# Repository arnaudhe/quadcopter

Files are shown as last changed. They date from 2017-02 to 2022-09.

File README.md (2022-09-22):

# Quadcopter

DIY quadcopter based on ESP32-WROOM



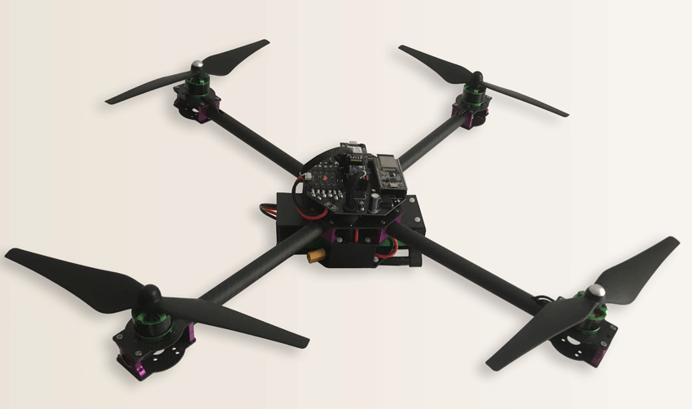
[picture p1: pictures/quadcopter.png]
Quadcopter picture Quadcopter


## Overview

### Architecture overview

```mermaid
  flowchart LR;
    subgraph QUADCOPTER
      BATTERY--supply-->Flight_controller
      BATTERY--supply-->GIMBAL
      HCSR04<--pulse-->ESP32
      subgraph Flight_controller
        MPU6050--I2C-->ESP32
        HMC5883L--I2C-->ESP32
        BMP280--I2C-->ESP32
        ESP32--DSHOT-->ESC
        ESP32--SPI-->SI4432
      end
      subgraph Motors
        ESC--3-->FRONT_RIGHT_MOTOR
        ESC--3-->FRONT_LEFT_MOTOR
        ESC--3-->REAR_RIGHT_MOTOR
        ESC--3-->REAR_LEFT_MOTOR
      end
      subgraph Video
        direction TB
        ESP32--PWM-->GIMBAL
        ESP32--TCP-->CAMERA
        CAMERA--Analog-->VIDEO_TX
        GIMBAL--supply-->VIDEO_TX
      end
      GPS--UART-->ESP32
    end
      subgraph Base_Station
        XBOX_REMOTE--USB-->LAPTOP
        LAPTOP<--USB-->RADIO_DONGLE
        VIDEO_RX--USB-->LAPTOP
      end
      RADIO_DONGLE-.433 MHz FSK.->SI4432
      LAPTOP-.WIFI.->ESP32
      VIDEO_TX-.5,8GHz.->VIDEO_RX
```

### Sensors

* Attitude sensing is based on MPU6050 (accelerometer + gyroscope) and HMC5883L (magnetometer), computed through a [Madgwick Filter](https://x-io.co.uk/open-source-imu-and-ahrs-algorithms/)
* Height sensing is based on vertical linear acceleration (output of attitude filter), a BMP180 (barometer) and a HCSR04 (ultrasound range sensor), computed through a [Kalman filter](https://en.wikipedia.org/wiki/Kalman_filter)
* Position sensing is base on horizontal linear acceleration (output of attitude filter) and a GPS, computed through a Kalman filter [Kalman filter](https://en.wikipedia.org/wiki/Kalman_filter)

cf. [documents](https://github.com/arnaudhe/quadcopter/tree/master/documents) for more details

### Controllers

* Attitude controller (manual mode) is based on a 4-dimensions [PID](https://en.wikipedia.org/wiki/PID_controller) (roll, pitch, yaw, height)
* Position controller (autonomous mode) is based on a 3-dimensions [PID](https://en.wikipedia.org/wiki/PID_controller) (x, y, z) which drives attitude controller

BLDC motors control is based on a commercial 4-in-1 ESC (electronic speed controller)

cf. [documents](https://github.com/arnaudhe/quadcopter/tree/master/documents) for more details

### Camera

The quadcopter is designed to support a [YI action camera](https://www.yitechnology.com/yi-action-camera), hold on a [2D Gimbal](https://hobbyking.com/fr_fr/tarot-t-2d-v2-xiaomi-yi-sports-camera-brushless-camera-gimbal-and-zyx22-controller.html).

The camera has:
* A TCP interface which supports json commands (take a picture, start recording, list files, ...)
* A streaming RTSP server which can be used for live video preview

The gimbal angles can be driven by the ESP32 through a serial interface.

### Communication

Communication between base station (computer or remote) is based on a shared data model, definied in a json file.

The data model ressources are implemented by the quadcopter and can be read/written/notified via:
* a json protocol (better for debug, high bandwith medium)
* a binary protocol (better for release, low bandwidth medium)

Two communications media are supported by the quadcopter:
* wifi (low range, hight bandwidth)
* FSK (longer range, low bandwidth)

```mermaid
  flowchart TD;
      subgraph Flight controller
      ESP32<-->WIFI;
      ESP32<-->RADIO;
      end
      WIFI--TCP/JSON-->CAMERA;
      CAMERA--Analog Video-->VTX
      VTX-->BASE_STATION
      WIFI<--UDP/JSON-->BASE_STATION
      RADIO<--FSK/BINARY-->BASE_STATION
```

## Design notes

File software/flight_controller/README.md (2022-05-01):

# Flight Controller

## Overview

The flight controller firmware runs on a ESP32, on a ESP32-WROOM development board.

This boards embeds an ESP32-VROOM module (which contains ESP32 MCU + wifi + BLE + flash), a power supply, a usb-serial interface, and a micro-USB port.

The project is based on Espressif's official [ESP-IDF SDK](https://github.com/espressif/esp-idf), which comes with many components (FreeRTOS, LwIP, utilities, ...). This third-party sdk is actually integrated as a git sumbodule.

## Setup

Flight controller SDK setup is managed by parent folder `software`, refer to its README

## Build, flash, monitor

### Setup the environement

```
# source ../env.sh
```

### Build

```
# idf.py build
```

### Flash

```
# idf.py flash [-p <port>]
```

### Monitor

```
# idf.py monitor [-p <port>]
```
Hit `ctrl + $` to exit

You can alternatively use any serial port util at 921600 bauds

## Visual Studio Code integration

Previous commands are configured as Visual Studio Code tasks.

Refer to parent folder READLE to setup Visual Studio Code and run those tasks

Then, hit `cmd + shift + B` to build the project. The errors and warnings should be highlighted in the "problems" tab.

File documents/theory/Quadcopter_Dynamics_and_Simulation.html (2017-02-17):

# Andrew Gibiansky :: Math → [Code] (http://andrew.gibiansky.com/)

# Quadcopter Dynamics and Simulation

Friday, November 23, 2012

# Introduction

A helicopter is a flying vehicle which uses rapidly spinning rotors to push air downwards, thus creating a thrust force keeping the helicopter aloft. Conventional helicopters have two rotors. These can be arranged as two coplanar rotors both providing upwards thrust, but spinning in opposite directions (in order to balance the torques exerted upon the body of the helicopter). The two rotors can also be arranged with one main rotor providing thrust and a smaller side rotor oriented laterally and counteracting the torque produced by the main rotor. However, these configurations require complicated machinery to control the direction of motion; a swashplate is used to change the angle of attack on the main rotors. In order to produce a torque the angle of attack is modulated by the location of each rotor in each stroke, such that more thrust is produced on one side of the rotor plane than the other. The complicated design of the rotor and swashplate mechanism presents some problems, increasing construction costs and design complexity.

A quadrotor helicopter (quadcopter) is a helicopter which has four equally spaced rotors, usually arranged at the corners of a square body. With four independent rotors, the need for a swashplate mechanism is alleviated. The swashplate mechanism was needed to allow the helicopter to utilize more degrees of freedom, but the same level of control can be obtained by adding two more rotors.

The development of quadcopters has stalled until very recently, because controlling four independent rotors has proven to be incredibly difficult and impossible without electronic assistance. The decreasing cost of modern microprocessors has made electronic and even completely autonomous control of quadcopters feasible for commercial, military, and even hobbyist purposes.

Quadcopter control is a fundamentally difficult and interesting problem. With six degrees of freedom (three translational and three rotational) and only four independent inputs (rotor speeds), quadcopters are severely underactuated. In order to achieve six degrees of freedom, rotational and translational motion are coupled. The resulting dynamics are highly nonlinear, especially after accounting for the complicated aerodynamic effects. Finally, unlike ground vehicles, helicopters have very little friction to prevent their motion, so they must provide their own damping in order to stop moving and remain stable. Together, these factors create a very interesting control problem. We will present a very simplified model of quadcopter dynamics and design controllers for our dynamics to follow a designated trajectory. We will then test our controllers with a numerical simulation of a quadcopter in flight.

# Quadcopter Dynamics

We will start deriving quadcopter dynamics by introducing the two frames in which will operate. The inertial frame is defined by the ground, with gravity pointing in the negative zz direction. The body frame is defined by the orientation of the quadcopter, with the rotor axes pointing in the positive zz direction and the arms pointing in the xx and yy directions.

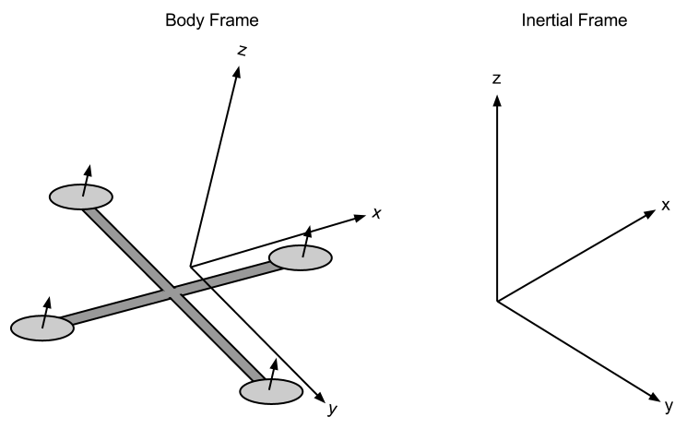
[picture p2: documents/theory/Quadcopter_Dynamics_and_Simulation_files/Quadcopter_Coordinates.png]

Quadcopter Body Frame and Inertial Frame

## Kinematics

Before delving into the physics of quadcopter motion, let us formalize the kinematics in the body and inertial frames. We define the position and velocity of the quadcopter in the inertial frame as x=(x,y,z)Tx=(x,y,z)T and x˙=(x˙,y˙,z˙)Tx˙=(x˙,y˙,z˙)T, respectively. Similarly, we define the roll, pitch, and yaw angles in the body frame as θ=(ϕ,θ,ψ)Tθ=(ϕ,θ,ψ)T, with corresponding angular velocities equal to θ˙=(ϕ˙,θ˙,ψ˙)Tθ˙=(ϕ˙,θ˙,ψ˙)T. However, note that the angular velocity vector ω≠θ˙ω≠θ˙. The angular velocity is a vector pointing along the axis of rotation, while θ˙θ˙ is just the time derivative of yaw, pitch, and roll. In order to convert these angular velocities into the angular velocity vector, we can use the following relation:

ω=⎡⎣⎢⎢⎢1000cϕ−sϕ−sθcθsϕcθcϕ⎤⎦⎥⎥⎥θ˙ω=[10−sθ0cϕcθsϕ0−sϕcθcϕ]θ˙

where ωω is the angular velocity vector in the body frame.

We can relate the body and inertial frame by a rotation matrix RR which goes from the body frame to the inertial frame. This matrix is derived by using the ZYZ Euler angle conventions and successively “undoing” the yaw, pitch, and roll.

R=⎡⎣⎢⎢⎢cϕcψ−cθsϕsψcθcψsϕ+cϕsψsϕsθ−cψsϕ−cϕcθsψcϕcθcψ−sϕsψcϕsθsθsψ−cψsθcθ⎤⎦⎥⎥⎥R=[cϕcψ−cθsϕsψ−cψsϕ−cϕcθsψsθsψcθcψsϕ+cϕsψcϕcθcψ−sϕsψ−cψsθsϕsθcϕsθcθ]

For a given vector v⃗ v→ in the body frame, the corresponding vector is given by Rv⃗ Rv→ in the inertial frame.

## Physics

In order to properly model the dynamics of the system, we need an understanding of the physical properties that govern it. We will begin with a description of the motors being used for our quadcopter, and then use energy considerations to derive the forces and thrusts that these motors produce on the entire quadcopter. All motors on the quadcopter are identical, so we can analyze a single one without loss of generality. Note that adjacent propellers, however, are oriented opposite each other; if a propeller is spinning “clockwise”, then the two adjacent ones will be spinning “counter-clockwise”, so that torques are balanced if all propellers are spinning at the same rate.

### Motors

Brushless motors are used for all quadcopter applications. For our electric motors, the torque produced is given by

τ=Kt(I−I0)τ=Kt(I−I0)

where ττ is the motor torque, II is the input current, I0I0 is the current when there is no load on the motor, and KtKt is the torque proportionality constant. The voltage across the motor is the sum of the back-EMF and some resistive loss:

V=IRm+KvωV=IRm+Kvω

where VV is the voltage drop across the motor, RmRm is the motor resistance, ωω is the angular velocity of the motor, and KvKv is a proportionality constant (indicating back-EMF generated per RPM). We can use this description of our motor to calculate the power it consumes. The power is

P=IV=(τ+KtI0)(KtI0Rm+τRm+KtKvω)Kt2P=IV=(τ+KtI0)(KtI0Rm+τRm+KtKvω)Kt2

For the purposes of our simple model, we will assume a negligible motor resistance. Then, the power becomes proportional to the angular velocity:

P≈(τ+KtI0)KvωKtP≈(τ+KtI0)KvωKt

Further simplifying our model, we assume that KtI0≪τKtI0≪τ. This is not altogether unreasonable, since I0I0 is the current when there is no load, and is thus rather small. In practice, this approximation holds well enough. Thus, we obtain our final, simplified equation for power:

P≈KvKtτω.P≈KvKtτω.

### Forces

The power is used to keep the quadcopter aloft. By conservation of energy, we know that the energy the motor expends in a given time period is equal to the force generated on the propeller times the distance that the air it displaces moves (P⋅dt=F⋅dxP⋅dt=F⋅dx). Equivalently, the power is equal to the thrust times the air velocity (P=FdxdtP=Fdxdt).

P=TvhP=Tvh

We assume vehicle speeds are low, so vhvh is the air velocity when hovering. We also assume that the free stream velocity, v∞v∞, is zero (the air in the surrounding environment is stationary relative to the quadcopter). Momentum theory gives us the equation for hover velocity as a function of thrust,

vh=T2ρA‾‾‾‾‾√vh=T2ρA

where ρρ is the density of the surrounding air and AA is the area swept out by the rotor. Using our simplified equation for power, we can then write

P=KvKtτω=KvKτKtTω=T322ρA‾‾‾‾√.P=KvKtτω=KvKτKtTω=T322ρA.

Note that in the general case, τ=r⃗ ×F⃗ τ=r→×F→; in this case, the torque is proportional to the thrust TT by some constant ratio KτKτ determined by the blade configuration and parameters. Solving for the thrust magnitude TT, we obtain that thrust is proportional to the square of angular velocity of the motor:

T=(KvKτ2ρA‾‾‾‾√Ktω)2=kω2T=(KvKτ2ρAKtω)2=kω2

where kk is some appropriately dimensioned constant. Summing over all the motors, we find that the total thrust on the quadcopter (in the body frame) is given by

TB=∑i=14Ti=k⎡⎣⎢⎢⎢00∑ωi2⎤⎦⎥⎥⎥.TB=∑i=14Ti=k[00∑ωi2].

In addition to the thrust force, we will model friction as a force proportional to the linear velocity in each direction. This is a highly simplified view of fluid friction, but will be sufficient for our modeling and simulation. Our global drag forces will be modeled by an additional force term

FD=⎡⎣⎢⎢−kdx˙−kdy˙−kdz˙⎤⎦⎥⎥FD=[−kdx˙−kdy˙−kdz˙]

If additional precision is desired, the constant kdkd can be separated into three separate friction constants, one for each direction of motion. If we were to do this, we would want to model friction in the body frame rather than the inertial frame.

### Torques

Now that we have computed the forces on the quadcopter, we would also like to compute the torques. Each rotor contributes some torque about the body zz axis. This torque is the torque required to keep the propeller spinning and providing thrust; it creates the instantaneous angular acceleration and overcomes the frictional drag forces. The drag equation from fluid dynamics gives us the frictional force:

FD=12ρCDAv2.FD=12ρCDAv2.

where ρρ is the surrounding fluid density, AA is the reference area (propeller cross-section, not area swept out by the propeller), and CDCD is a dimensionless constant. This, while only accurate in some in some cases, is good enough for our purposes. This implies that the torque due to drag is given by

τD=12RρCDAv2=12RρCDA(ωR)2=bω2τD=12RρCDAv2=12RρCDA(ωR)2=bω2

where ωω is the angular velocity of the propeller, RR is the radius of the propeller, and bb is some appropriately dimensioned constant. Note that we’ve assumed that all the force is applied at the tip of the propeller, which is certainly inaccurate; however, the only result that matters for our purposes is that the drag torque is proportional to the square of the angular velocity. We can then write the complete torque about the zz axis for the iith motor:

τz=bω2+IMω˙τz=bω2+IMω˙

where IMIM is the moment of inertia about the motor zz axis, ω˙ω˙ is the angular acceleration of the propeller, and bb is our drag coefficient. Note that in steady state flight (i.e. not takeoff or landing), ω˙≈0ω˙≈0, since most of the time the propellers will be maintaining a constant (or almost constant) thrust and won’t be accelerating. Thus, we ignore this term, simplifying the entire expression to

τz=(−1)i+1bωi2.τz=(−1)i+1bωi2.

where the (−1)i+1(−1)i+1 term is positive for the iith propeller if the propeller is spinning clockwise and negative if it is spinning counterclockwise. The total torque about the zz axis is given by the sum of all the torques from each propeller:

τψ=b(ω12−ω22+ω32−ω42)τψ=b(ω12−ω22+ω32−ω42)

The roll and pitch torques are derived from standard mechanics. We can arbitrarily choose the i=1i=1 and i=3i=3 motors to be on the roll axis, so

τϕ=∑r×T=L(kω12−kω32)=Lk(ω12−ω32)τϕ=∑r×T=L(kω12−kω32)=Lk(ω12−ω32)

Correspondingly, the pitch torque is given by a similar expression

τθ=Lk(ω22−ω42)τθ=Lk(ω22−ω42)

where LL is the distance from the center of the quadcopter to any of the propellers. All together, we find that the torques in the body frame are

τB=⎡⎣⎢⎢⎢Lk(ω12−ω32)Lk(ω22−ω42)b(ω12−ω22+ω32−ω42)⎤⎦⎥⎥⎥τB=[Lk(ω12−ω32)Lk(ω22−ω42)b(ω12−ω22+ω32−ω42)]

The model we’ve derived so far is highly simplified. We ignore a multitude of advanced effects that contribute to the highly nonlinear dynamics of a quadcopter. We ignore rotational drag forces (our rotational velocities are relatively low), blade flapping (deformation of propeller blades due to high velocities and flexible materials), surrounding fluid velocities (wind), etc. With that said, we now have all the parts necessary to write out the dynamics of our quadcopter.

### Equations of Motion

In the inertial frame, the acceleration of the quadcopter is due to thrust, gravity, and linear friction. We can obtain the thrust vector in the inertial frame by using our rotation matrix RR to map the thrust vector from the body frame to the inertial frame. Thus, the linear motion can be summarized as

mx¨=⎡⎣⎢⎢00−mg⎤⎦⎥⎥+RTB+FDmx¨=[00−mg]+RTB+FD

where x⃗ x→ is the position of the quadcopter, gg is the acceleration due to gravity, FDFD is the drag force, and TBTB is the thrust vector in the body frame. While it is convenient to have the linear equations of motion in the inertial frame, the rotational equations of motion are useful to us in the body frame, so that we can express rotations about the center of the quadcopter instead of about our inertial center. We derive the rotational equations of motion from Euler’s equations for rigid body dynamics. Expressed in vector form, Euler’s equations are written as

Iω˙+ω×(Iω)=τIω˙+ω×(Iω)=τ

where ωω is the angular velocity vector, II is the inertia matrix, and ττ is a vector of external torques. We can rewrite this as

ω˙=⎡⎣⎢⎢⎢ω˙xω˙yω˙z⎤⎦⎥⎥⎥=I−1(τ−ω×(Iω)).ω˙=[ω˙xω˙yω˙z]=I−1(τ−ω×(Iω)).

We can model our quadcopter as two thin uniform rods crossed at the origin with a point mass (motor) at the end of each. With this in mind, it’s clear that the symmetries result in a diagonal inertia matrix of the form

I=⎡⎣⎢⎢⎢Ixx000Iyy000Izz⎤⎦⎥⎥⎥.I=[Ixx000Iyy000Izz].

Therefore, we obtain our final result for the body frame rotational equations of motion

ω˙=⎡⎣⎢⎢⎢τϕIxx−1τθIyy−1τψIzz−1⎤⎦⎥⎥⎥−⎡⎣⎢⎢⎢⎢Iyy−IzzIxxωyωzIzz−IxxIyyωxωzIxx−IyyIzzωxωy⎤⎦⎥⎥⎥⎥ω˙=[τϕIxx−1τθIyy−1τψIzz−1]−[Iyy−IzzIxxωyωzIzz−IxxIyyωxωzIxx−IyyIzzωxωy]

# Simulation

Now that we have complete equations of motion describing the dynamics of the system, we can create a simulation environment in which to test and view the results of various inputs and controllers. Although more advanced methods are available, we can quickly write a simulator which utilizes Euler’s method for solving differential equations to evolve the system state. In MATLAB, this simulator would be written as follows.

% Simulation times, in seconds.
start_time = 0;
end_time = 10;
dt = 0.005;
times = start_time:dt:end_time;

% Number of points in the simulation.
N = numel(times);

% Initial simulation state.
x = [0; 0; 10];
xdot = zeros(3, 1);
theta = zeros(3, 1);

% Simulate some disturbance in the angular velocity.
% The magnitude of the deviation is in radians / second.
deviation = 100;
thetadot = deg2rad(2 * deviation * rand(3, 1) - deviation);

% Step through the simulation, updating the state.
for t = times
    % Take input from our controller.
    i = input(t);

    omega = thetadot2omega(thetadot, theta);

    % Compute linear and angular accelerations.
    a = acceleration(i, theta, xdot, m, g, k, kd);
    omegadot = angular_acceleration(i, omega, I, L, b, k);

    omega = omega + dt * omegadot;
    thetadot = omega2thetadot(omega, theta); 
    theta = theta + dt * thetadot;
    xdot = xdot + dt * a;
    x = x + dt * xdot;
end

We would then need functions to compute all of the physical forces and torques.

% Compute thrust given current inputs and thrust coefficient.
function T = thrust(inputs, k)
    % Inputs are values for ${\omega_i}^2$
    T = [0; 0; k * sum(inputs)];
end

% Compute torques, given current inputs, length, drag coefficient, and thrust coefficient.
function tau = torques(inputs, L, b, k)
    % Inputs are values for ${\omega_i}^2$
    tau = [
        L * k * (inputs(1) - inputs(3))
        L * k * (inputs(2) - inputs(4))
        b * (inputs(1) - inputs(2) + inputs(3) - inputs(4))
    ];
end

function a = acceleration(inputs, angles, xdot, m, g, k, kd)
    gravity = [0; 0; -g];
    R = rotation(angles);
    T = R * thrust(inputs, k);
    Fd = -kd * xdot;
    a = gravity + 1 / m * T + Fd;
end

function omegadot = angular_acceleration(inputs, omega, I, L, b, k)
    tau = torques(inputs, L, b, k);
    omegaddot = inv(I) * (tau - cross(omega, I * omega));
end

We would also need values for all of our physical constants, a function to compute the rotation matrix RR, and functions to convert from an angular velocity vector ωω to the derivatives of roll, pitch, and yaw and vice-versa. These are not shown. We can then draw the quadcopter in a three-dimensional visualization which is updated as the simulation is running.

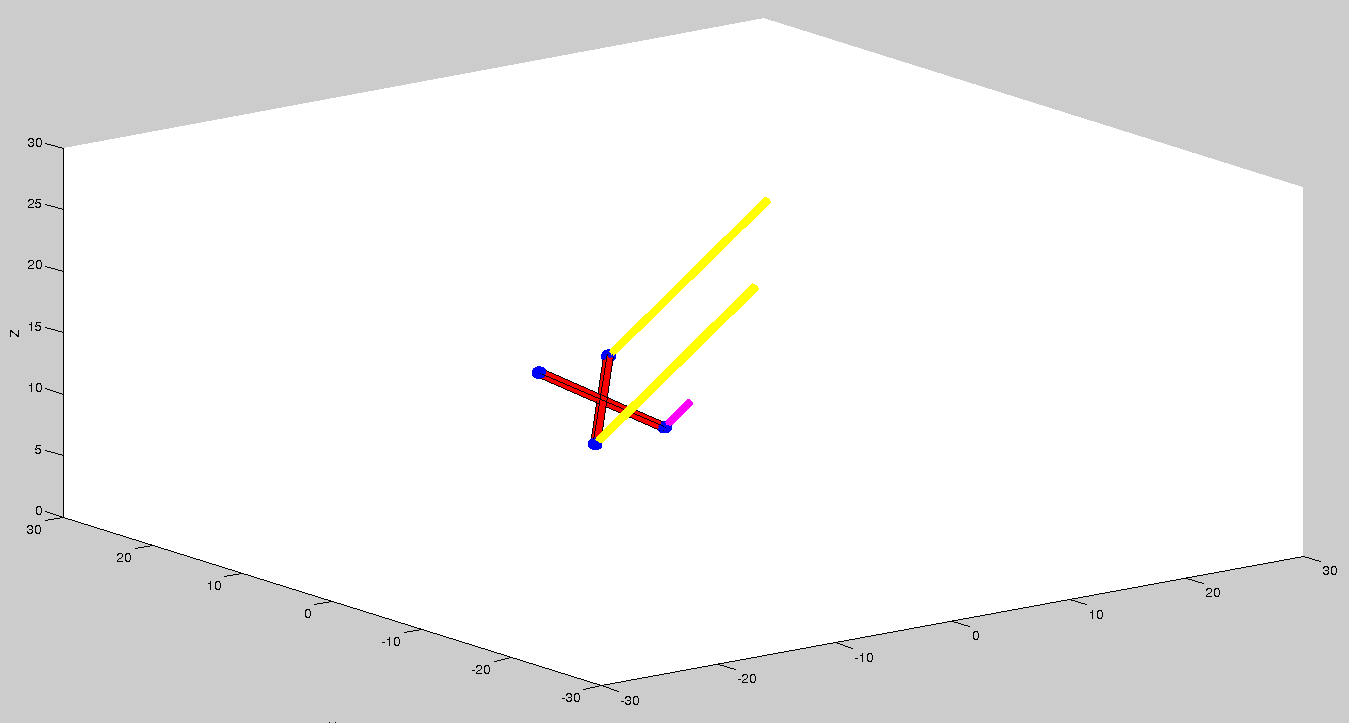
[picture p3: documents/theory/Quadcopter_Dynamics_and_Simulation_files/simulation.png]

Quadcopter Simulation. Bars above each propeller represent, roughly, relative thrust magnitudes.

# Control

The purpose of deriving a mathematical model of a quadcopter is to assist in developing controllers for physical quadcopters. The inputs to our system consist of the angular velocities of each rotor, since all we can control is the voltages across the motors. Note that in our simplified model, we only use the square of the angular velocities, ωi2ωi2, and never the angular velocity itself, ωiωi. For notational simplicity, let us introduce the inputs γi=ωi2γi=ωi2. Since we can set ωiωi, we can clearly set γiγi as well. With this, we can write our system as a first order differential equation in state space. Let x1x1 be the position in space of the quadcopter, x2x2 be the quadcopter linear velocity, x3x3 be the roll, pitch, and yaw angles, and x4x4 be the angular velocity vector. (Note that all of these are 3-vectors.) With these being our state, we can write the state space equations for the evolution of our state.

x1˙x2˙x3˙x4˙=x2=⎡⎣⎢⎢00−g⎤⎦⎥⎥+1mRTB+1mFD=⎡⎣⎢⎢⎢1000cϕ−sϕ−sθcθsϕcθcϕ⎤⎦⎥⎥⎥−1x4=⎡⎣⎢⎢⎢τϕIxx−1τθIyy−1τψIzz−1⎤⎦⎥⎥⎥−⎡⎣⎢⎢⎢⎢Iyy−IzzIxxωyωzIzz−IxxIyyωxωzIxx−IyyIzzωxωy⎤⎦⎥⎥⎥⎥x1˙=x2x2˙=[00−g]+1mRTB+1mFDx3˙=[10−sθ0cϕcθsϕ0−sϕcθcϕ]−1x4x4˙=[τϕIxx−1τθIyy−1τψIzz−1]−[Iyy−IzzIxxωyωzIzz−IxxIyyωxωzIxx−IyyIzzωxωy]

Note that our inputs are not used in these equations directly. However, as we will see, we can choose values for ττ and TT, and then solve for values of γiγi.

## PD Control

In order to control the quadcopter, we will use a PD control, with a component proportional to the error between our desired trajectory and the observed trajectory, and a component proportional to the derivative of the error. Our quadcopter will only have a gyro, so we will only be able to use the angle derivatives ϕ˙ϕ˙, θ˙θ˙, and ψ˙ψ˙ in our controller; these measured values will give us the derivative of our error, and their integral will provide us with the actual error. We would like to stabilize the helicopter in a horizontal position, so our desired velocities and angles will all be zero. Torques are related to our angular velocities by τ=Iθ¨τ=Iθ¨, so we would like to set the torques proportional to the output of our controller, with τ=Iu(t)τ=Iu(t). Thus,

⎡⎣⎢⎢⎢τϕτθτψ⎤⎦⎥⎥⎥=⎡⎣⎢⎢⎢⎢⎢−Ixx(Kdϕ˙+Kp∫T0ϕ˙dt)−Iyy(Kdθ˙+Kp∫T0θ˙dt)−Izz(Kdψ˙+Kp∫T0ψ˙dt)⎤⎦⎥⎥⎥⎥⎥[τϕτθτψ]=[−Ixx(Kdϕ˙+Kp∫0Tϕ˙dt)−Iyy(Kdθ˙+Kp∫0Tθ˙dt)−Izz(Kdψ˙+Kp∫0Tψ˙dt)]

We have previously derived the relationship between torque and our inputs, so we know that

τB=⎡⎣⎢⎢Lk(γ1−γ3)Lk(γ2−γ4)b(γ1−γ2+γ3−γ4)⎤⎦⎥⎥=⎡⎣⎢⎢⎢⎢⎢−Ixx(Kdϕ˙+Kp∫T0ϕ˙dt)−Iyy(Kdθ˙+Kp∫T0θ˙dt)−Izz(Kdψ˙+Kp∫T0ψ˙dt)⎤⎦⎥⎥⎥⎥⎥τB=[Lk(γ1−γ3)Lk(γ2−γ4)b(γ1−γ2+γ3−γ4)]=[−Ixx(Kdϕ˙+Kp∫0Tϕ˙dt)−Iyy(Kdθ˙+Kp∫0Tθ˙dt)−Izz(Kdψ˙+Kp∫0Tψ˙dt)]

This gives us a set of three equations with four unknowns. We can constrain this by enforcing the constraint that our inputs must keep the quadcopter aloft:

T=mg.T=mg.

Note that this equation ignores the fact that the thrust will not be pointed directly up. This will limit the applicability of our controller, but should not cause major problems for small deviations from stability. If we had a way of determining the current angle accurately, we could compensate. If our gyro is precise enough, we can integrate the values obtained from the gyro to get the angles θθ and ϕϕ. In this case, we can calculate the thrust necessary to keep the quadcopter aloft by projecting the thrust mgmg onto the inertial zz axis. We find that

Tproj=mgcosθcosϕTproj=mgcos⁡θcos⁡ϕ

Therefore, with a precise angle measurement, we can instead enforce the requirement that the thrust be equal to

T=mgcosθcosϕT=mgcos⁡θcos⁡ϕ

in which case the component of the thrust pointing along the positive zz axis will be equal to mgmg. We know that the thrust is proportional to a weighted sum of the inputs:

T=mgcosθcosϕ=k∑γi⟹∑γi=mgkcosθcosϕT=mgcos⁡θcos⁡ϕ=k∑γi⟹∑γi=mgkcos⁡θcos⁡ϕ

With this extra constraint, we have a set of four linear equations with four unknowns γiγi. We can then solve for each γiγi, and obtain the following input values:

γ1γ2γ3γ4=mg4kcosθcosϕ−2beϕIxx+eψIzzkL4bkL=mg4kcosθcosϕ+eψIzz4b−eθIyy2kL=mg4kcosθcosϕ−−2beϕIxx+eψIzzkL4bkL=mg4kcosθcosϕ+eψIzz4b+eθIyy2kLγ1=mg4kcos⁡θcos⁡ϕ−2beϕIxx+eψIzzkL4bkLγ2=mg4kcos⁡θcos⁡ϕ+eψIzz4b−eθIyy2kLγ3=mg4kcos⁡θcos⁡ϕ−−2beϕIxx+eψIzzkL4bkLγ4=mg4kcos⁡θcos⁡ϕ+eψIzz4b+eθIyy2kL

This is a complete specification for our PD controller. We can simulate this controller using our simulation environment. The controller drives the angular velocities and angles to zero.

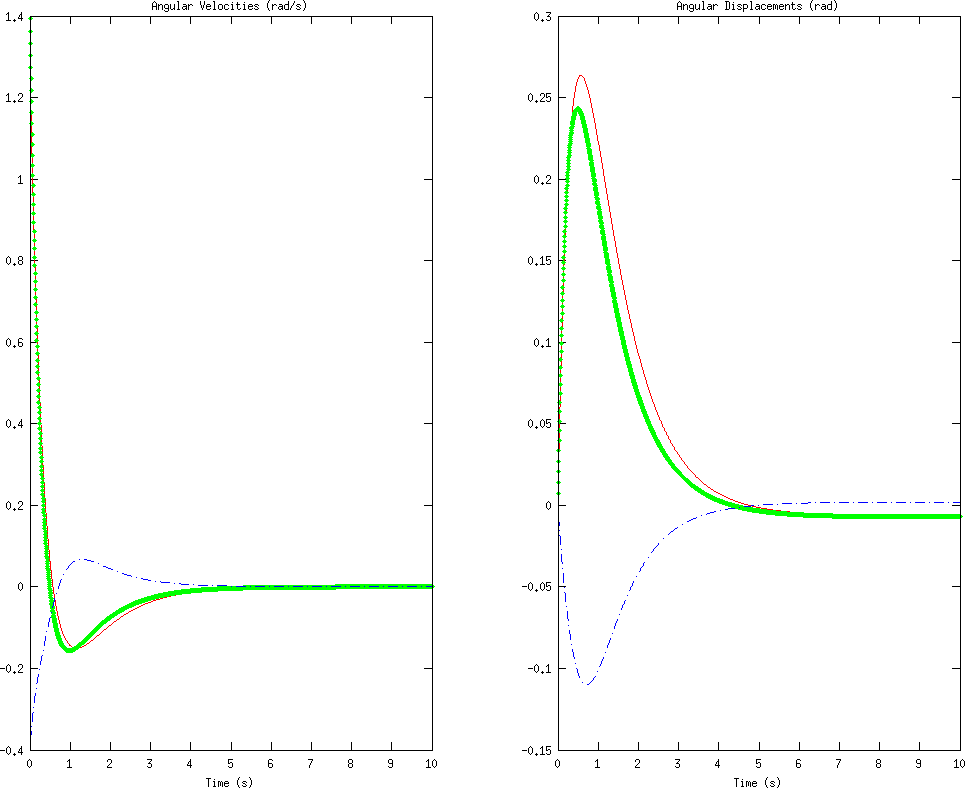
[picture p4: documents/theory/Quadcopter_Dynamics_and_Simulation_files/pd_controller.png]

Left: Angular velocities. Right: angular displacements. ϕϕ, θθ, ψψ are coded as red, green, and blue.

However, note that the angles are not completely driven to zero. The average steady state error (error after 10 seconds of simulation) is approximately 0.3∘∘. This is a common problem with using PD controllers for mechanical systems, and can be partially alleviated with a PID controller, as we will discuss in the next section.

In addition, note that since we are only controlling angular velocities, our positions and linear velocities do not converge to zero. However, the zz position will remain constant, because we have constrained the total vertical thrust to be such that it keeps the quadcopter perfectly aloft, without ascending or descending. However, this is really nothing more than a curiosity. With the limited sensing that we have available to us, there is nothing we can do to control the linear position and velocity of the quadcopter. While in theory we could compute the linear velocities and positions from the angular velocities, in practice the values will be so noisy as to be completely useless. Thus, we will restrict ourselves to just stabilizing the quadcopter angle and angular velocity. (Traditionally, navigation is done by a human, and stabilization is there simply to make control easier for the human operator.)

We have implemented this PD control for use in our simulation. The controller is implemented as a function which is given some state (corresponding to controller state, not system state) and the sensor inputs, and must compute the inputs γiγi and the updated state. The code for a PD control follows.

% Compute system inputs and updated state.
% Note that input = [$\gamma_1$, $\ldots$, $\gamma_4$]
function [input, state] = pd_controller(state, thetadot)
    % Controller gains, tuned by hand and intuition.
    Kd = 4;
    Kp = 3;

    % Initialize the integral if necessary.
    if ~isfield(state, 'integral')
        params.integral = zeros(3, 1);
    end

    % Compute total thrust
    total = state.m * state.g / state.k / (cos(state.integral(1)) * cos(state.integral(2)));

    % Compute errors
    e = Kd * thetadot + Kp * params.integral;

    % Solve for the inputs, $\gamma_i$
    input = error2inputs(params, accels, total);

    % Update the state
    params.integral = params.integral + params.dt .* thetadot;
end

## PID Control

PD controllers are nice in their simplicity and ease of implementation, but they are often inadequate for controlling mechanical systems. Especially in the presence of noise and disturbances, PD controllers will often lead to steady state error. A PID control is a PD control with another term added, which is proportional to the integral of the process variable. Adding an integral term causes any remaining steady-state error to build up and enact a change, so a PID controller should be able to track our trajectory (and stabilize the quadcopter) with a significantly smaller steady-state error. The equations remain identical to the ones presented in the PD case, but with an additional term in the error:

eϕeθeψ=Kdϕ˙+Kp∫T0ϕ˙dt+Ki∫T0∫T0ϕ˙dtdt=Kdθ˙+Kp∫T0θ˙dt+Ki∫T0∫T0θ˙dtdt=Kdψ˙+Kp∫T0ψ˙dt+Ki∫T0∫T0ψ˙dtdteϕ=Kdϕ˙+Kp∫0Tϕ˙dt+Ki∫0T∫0Tϕ˙dtdteθ=Kdθ˙+Kp∫0Tθ˙dt+Ki∫0T∫0Tθ˙dtdteψ=Kdψ˙+Kp∫0Tψ˙dt+Ki∫0T∫0Tψ˙dtdt

However, PID controls come with their own shortcomings. One problem that commonly occurs with a PID control is known as integral windup.

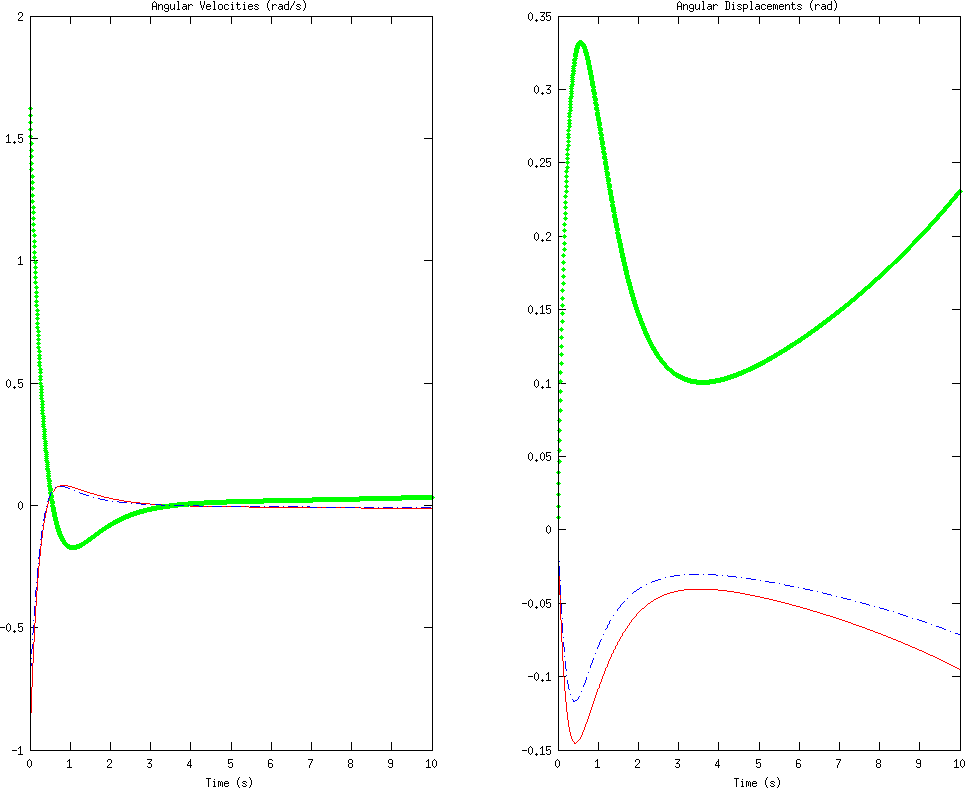
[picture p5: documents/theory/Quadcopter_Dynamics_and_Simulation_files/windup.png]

In some cases, integral wind-up can cause lengthy oscillations instead of settling. In other cases, wind-up may actually cause the system to become unstable, instead of taking longer to reach a steady state.

If there is a large disturbance in the process variable, this large disturbance is integrated over time, becoming a still larger control signal (due to the integral term). However, even once the system stabilizes, the integral is still large, thus causing the controller to overshoot its target. It may then begin a series of dieing down oscillations, become unstable, or simply take an incredibly long time to reach a steady state. In order to avoid this, we disable the integral function until we reach something close to the steady state. Once we are in a controllable region near the desired steady state, we turn on the integral function, which pushes the system towards a low steady-state error.

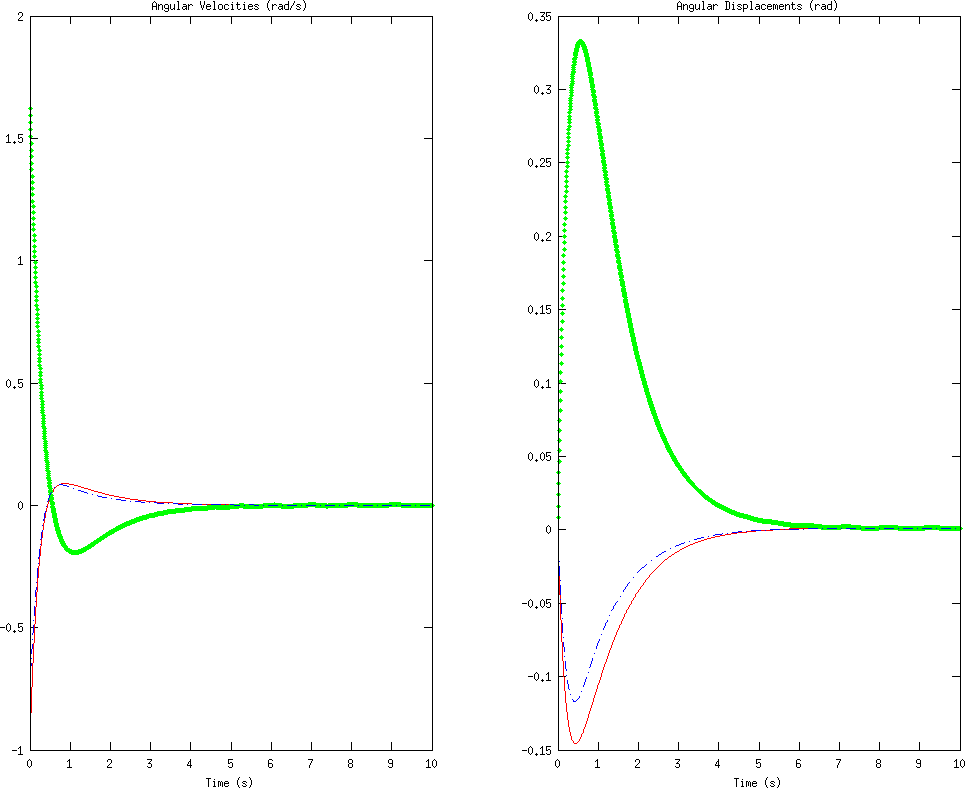
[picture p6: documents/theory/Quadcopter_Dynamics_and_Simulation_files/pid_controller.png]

With a properly implemented PID, we achieve an error of approximately 0.06∘∘ after 10 seconds.

We have implemented this PID control for use in simulation, in the same way as with the PD controller shown earlier. Note that there is an additional parameter to tune in a PID. The disturbances used for all the test cases are identical, shown to compare the controllers.

% Compute system inputs and updated state.
% Note that input = [$\gamma_1$, $\ldots$, $\gamma_4$]
function [input, state] = pid_controller(state, thetadot)
    % Controller gains, tuned by hand and intuition.
    Kd = 4;
    Kp = 3;
    Ki = 5.5;

    % Initialize the integral if necessary.
    if ~isfield(state, 'integral')
        params.integral = zeros(3, 1);
        params.integral2 = zeros(3, 1);
    end

    % Prevent wind-up
    if max(abs(params.integral2)) > 0.01
        params.integral2(:) = 0;
    end

    % Compute total thrust
    total = state.m * state.g / state.k / (cos(state.integral(1)) * cos(state.integral(2)));

    % Compute errors
    e = Kd * thetadot + Kp * params.integral - Ki * params.integral2;

    % Solve for the inputs, $\gamma_i$
    input = error2inputs(params, accels, total);

    % Update the state
    params.integral = params.integral + params.dt .* thetadot;
    params.integral2 = params.integral2 + params.dt .* params.integral;
end

## Automatic PID Tuning

Although PID control has the potential to perform very well, it turns out that the quality of the controller is highly dependent on the gain parameters. Tuning the parameters by hand may be quite difficult, as the ratios of the parameters is as important as the magnitudes of the parameters themselves; often, tuning parameters requires detailed knowledge of the system and an understanding of the conditions in which the PID control will be used. The parameters we chose previously were tuned by hand for good performance, simply by running simulations with many possibly disturbances and parameter values, and choosing something that worked reasonably well. This method is clearly suboptimal, not only because it can be very difficult and labor-intensive (and sometimes more or less impossible) but also because the resulting gains are not in any way guaranteed to be optimal or even close to optimal.

Ideally, we would be able to use an algorithm to analyze a system and output the “optimal” PID gains, for some reasonable definition of optimal. This problem has been studied in depth, and many methods have been proposed. Many of these methods require detailed knowledge of the system being modeled, and some rely on properties of the system, such as stability or linearity. The method we will use for choosing our PID parameters is a method known as extremum seeking.

Extremum seeking works exactly as the name implies. We define the “optimal” set of parameters as some vector θ⃗ =(Kp,Ki,Kd)θ→=(Kp,Ki,Kd) which minimizes some cost function J(θ⃗ )J(θ→). In our case, we would like to define a cost function that penalizes high error and error over extended durations of time. One candidate cost function is given by

J(θ⃗ )=1tf−to∫tft0e(t,θ⃗ )2dtJ(θ→)=1tf−to∫t0tfe(t,θ→)2dt

where e(t,θ⃗ )e(t,θ→) is the error in following some reference trajectory with some initial disturbance using a set of parameters θ⃗ θ→. Suppose we were able to somehow compute the gradient of this cost function, ∇J(θ⃗ )∇J(θ→). In that case, we could iteratively improve our parameter vector by defining a parameter update rule

θ⃗ (k+1)=θ⃗ (k)−α∇J(θ⃗ )θ→(k+1)=θ→(k)−α∇J(θ→)

where θ⃗ (k)θ→(k) is the parameter vector after kk iterations and αα is some step size which dictates how much we adjust our parameter vector at each step of the iteration. As k→∞k→∞, the cost function J(θ⃗ )J(θ→) will approach a local minimum in the space of PID parameters.

The question remains as to how we can estimate ∇J(θ⃗ )∇J(θ→). By definition,

∇J(θ⃗ )=(∂∂KpJ(θ⃗ ),∂∂KiJ(θ⃗ ),∂∂KdJ(θ⃗ )).∇J(θ→)=(∂∂KpJ(θ→),∂∂KiJ(θ→),∂∂KdJ(θ→)).

We know how to compute J(θ⃗ )J(θ→). Using this, we can approximate the derivative with respect to any of the gains numerically, simply by computing

∂∂KJ(θ⃗ )≈J(θ⃗ +δ⋅û K)−J(θ⃗ −δ⋅û K)2δ∂∂KJ(θ→)≈J(θ→+δ⋅u^K)−J(θ→−δ⋅u^K)2δ

where û Ku^K is the unit vector in the KK direction. As δ→0δ→0, this approximation becomes better. Using this approximation, we can minimize our cost function and achieve locally optimal PID parameters. We can start with randomly initialized positive weights, disturb the system in some set manner, evaluate J(θ⃗ )J(θ→) by simulating the system for different PID parameters, and then compute the gradient. Then, using the method of gradient descent, we can iteratively oprtimize our gains until we have some form of convergence.

The gradient descent method does, however, have several problems. First of all, although it finds a local minimum, that minimum is only guaranteed to be a local minimum - there may be other minima which are better global minima. In order to avoid choosing suboptimal local minima in the cost function, we repeat our optimization several times, and choose the best result. We initialize our PID parameters randomly, so each time we run the optimization we will get a different result. In addition, instead of choosing disturbance and then optimizing the response to that disturbance, we use several random disturbances at each iteration and use the average response to compute costs and gradients. This ensures that our parameters are general and not optimized for a specific disturbance. In addition, we vary the step size and the number of disturbances to try per iteration, in order to increase the sensitivity of our results as our iteration continues. We stop iterations when we detect a steady state, which we do by computing a linear regression on the most recent costs and iterating until the slope is statistically indistinguishable from zero using a 99% confidence interval.

Using our quadcopter simulation, we can define a function that computes the cost for a given set of PID parameters.

function J = cost(theta)
    % Create a controller using the given gains.
    control = controller('pid', theta(1), theta(2), theta(3));

    % Perform a simulation.
    data = simulate(control);

    % Compute the integral, $\frac{1}{t_f - t_0} \int_{t_0}^{t_f} e(t)^2 dt$
    t0 = 0;
    tf = 1;
    J = 1/(tf - t0) * sum(data.theta(data.t >= t0 & data.t <= tf) .^ 2) * data.dt;
end

We can use this function to approximate a derivative with respect to a gain:

% Compute derivative with respect to first parameter.
delta = 0.01;
var = [1, 0, 0];
derivative = (cost(theta + delta * var) - cost(theta - delta * var)) / (2 * delta);

We can then use our gradient descent method (with all modifications described above) to minimize the cost function and obtain a good set of PID parameters. We can verify that our tuning method is working by visualizing the cost function versus the iteration number, and seeing that the cost function is indeed going down and stabilizing at a local minimum.

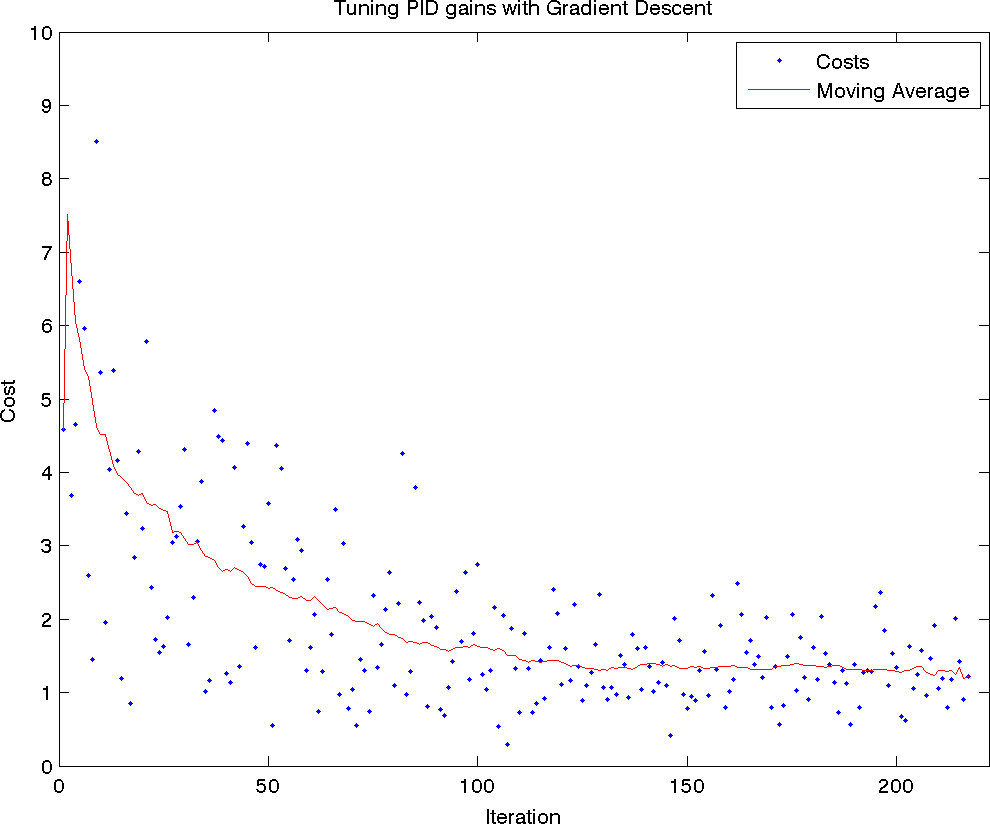
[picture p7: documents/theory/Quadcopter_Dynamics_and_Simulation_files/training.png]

Cost function plotted as a function of iteration number, along with moving average. Tuning stops when the slope of the moving average becomes statistically indistinguishable from zero with a 99% confidence interval.

We can compare the manually-chosen PID parameters with those designed by the algorithm.

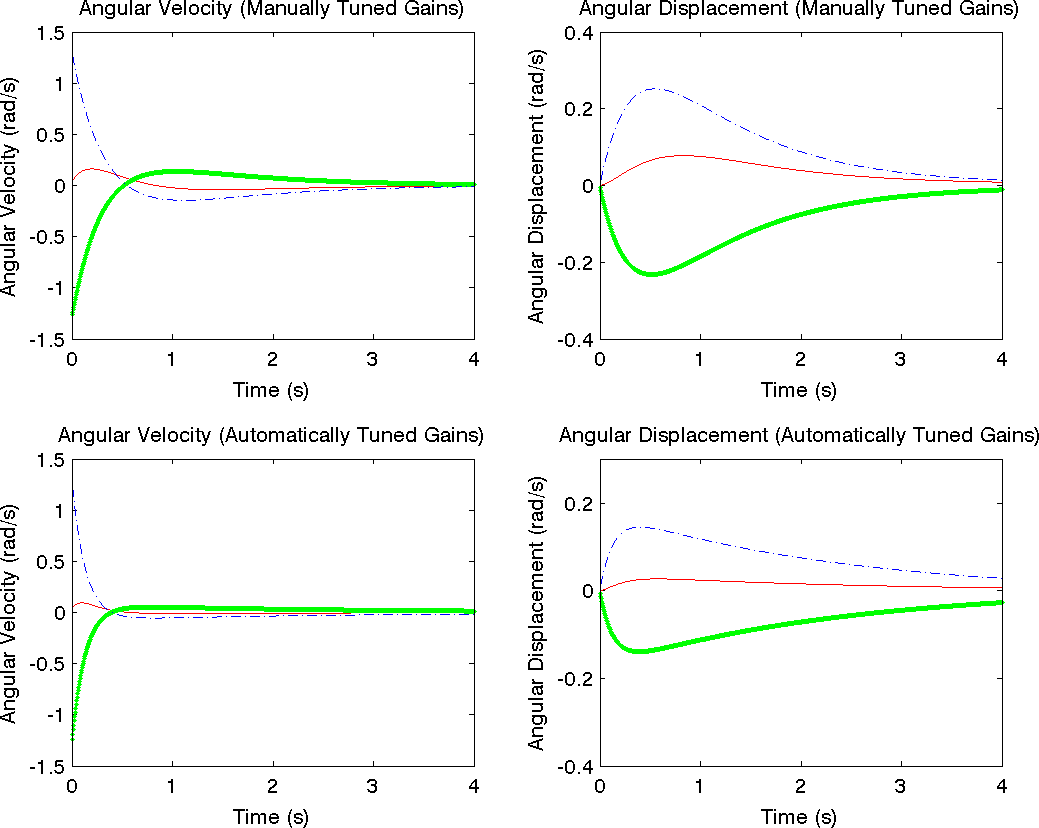
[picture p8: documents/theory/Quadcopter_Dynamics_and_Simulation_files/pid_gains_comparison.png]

Top: Angular velocities and angular displacements, using manually tuned PID controller. Bottom: Angular velocities and angular displacements, using automatically tuned PID controller.

The automatically-chosen PID parameters do significantly better overall. They have significantly smaller swings in value, overshoot significantly less, and converge faster. However, the error in the angular displacement takes longer to converge to zero with the automatically tuned parameters than with the manually turned parameters, although the initial convergence is much better when the parameters are chosen via gradient descent. This is due to the fact that our cost function emphasizes squared error, and thus gives priority to minimizing overall error magnitude rather than long-term convergence. We could easily modify our cost function to give higher priority to long-term error, in which case the automatically-tuned parameters are likely to do better.

# Conclusion

We derived equations of motion for a quadcopter, starting with the voltage-torque relation for the brushless motors and working through the quadcopter kinematics and dynamics. We ignored aerodynamical effects such as blade-flapping and non-zero free stream velocity, but included air friction as a linear drag force in all directions. We used the equations of motion to create a simulator in which to test and visualize quadcopter control mechanisms.

We began with a simple PD controller. Although the PD controller worked, it left a significant steady-state error. In order to decrease the steady-state error, we added an integral term in order to create a PID controller. We tested the PID controller (with minor modifications to prevent integral wind-up) and found that it was better at preventing steady-state error than the PD controller when presented with the same disturbances and using the same proportional and derivative gains. We also found that tuning the PID controller was difficult, and would often lead to an unstable system for unknown reasons. In order to avoid the difficulty of PID tuning and find the optimal set of parameters, we used a gradient-descent based extremum seeking method in order to numerically estimate gradients of a cost function in PID-parameter space and iteratively choose a set of parameters to minimize the cost function. We found that the resulting controller was significantly better than the one using manually turned parameters.

Friday, November 23, 2012 - Posted in physics (http://andrew.gibiansky.com/blog/categories/physics), simulations (http://andrew.gibiansky.com/blog/categories/simulations)

« The Digital State (http://andrew.gibiansky.com/blog/electrical-engineering/the-digital-state) Digital Design Tools: Verilog and HDLs » (http://andrew.gibiansky.com/blog/electrical-engineering/digital-design-tools-verilog-and-hdls)

# Contact

If you've got questions, comments, suggestions, or just want to talk, feel free to email me at andrew.gibiansky on Gmail.



# Recent Posts (RSS) (http://andrew.gibiansky.com/feed.rss)

- NRAM: Theano Implementation (http://andrew.gibiansky.com/blog/machine-learning/nram-2)
- NRAM: Neural Random Access Memory (http://andrew.gibiansky.com/blog/machine-learning/nram-1)
- jq Primer: Munging JSON Data (http://andrew.gibiansky.com/blog/command-line/jq-primer)
- Creating a Culture of Good Engineering (http://andrew.gibiansky.com/blog/thoughts/engineering-practices)
- Common Techniques in Molecular Biology (http://andrew.gibiansky.com/blog/genetics/technique-primers)
- CRISPR Gene Editing (http://andrew.gibiansky.com/blog/genetics/crispr)
- Quick Coding Intro to Neural Networks (http://andrew.gibiansky.com/blog/machine-learning/coding-intro-to-nns)
- Writing a SAT Solver (http://andrew.gibiansky.com/blog/verification/writing-a-sat-solver)
- Lattice Boltzmann Method (http://andrew.gibiansky.com/blog/physics/lattice-boltzmann-method)
- Finger Trees (http://andrew.gibiansky.com/blog/haskell/finger-trees)
- Abstraction in Haskell (Monoids, Functors, Monads) (http://andrew.gibiansky.com/blog/haskell/haskell-abstractions)
- Typeclasses: Polymorphism in Haskell (http://andrew.gibiansky.com/blog/haskell/haskell-typeclasses)
- Your First Haskell Application (with Gloss) (http://andrew.gibiansky.com/blog/haskell/haskell-gloss)
- Intro to Haskell Syntax (http://andrew.gibiansky.com/blog/haskell/haskell-syntax)
- Linguistics and Syntax (http://andrew.gibiansky.com/blog/linguistics/why-syntax)
- Speech Recognition with Neural Networks (http://andrew.gibiansky.com/blog/machine-learning/speech-recognition-neural-networks)
- Matrix Multiplication (http://andrew.gibiansky.com/blog/mathematics/matrix-multiplication)
- Recurrent Neural Networks (http://andrew.gibiansky.com/blog/machine-learning/recurrent-neural-networks)
- Gauss Newton Matrix (http://andrew.gibiansky.com/blog/machine-learning/gauss-newton-matrix)
- Convolutional Neural Networks (http://andrew.gibiansky.com/blog/machine-learning/convolutional-neural-networks)
- Fully Connected Neural Network Algorithms (http://andrew.gibiansky.com/blog/machine-learning/fully-connected-neural-networks)
- Hessian Free Optimization (http://andrew.gibiansky.com/blog/machine-learning/hessian-free-optimization)
- Conjugate Gradient (http://andrew.gibiansky.com/blog/machine-learning/conjugate-gradient)
- Gradient Descent Typeclasses in Haskell (http://andrew.gibiansky.com/blog/machine-learning/gradient-descent)
- Homophony Groups in Haskell (http://andrew.gibiansky.com/blog/linguistics/homophony-groups)
- Creating Language Kernels for IPython (http://andrew.gibiansky.com/blog/ipython/ipython-kernels)
- Detecting Genetic Copynumber with Gaussian Mixture Models (http://andrew.gibiansky.com/blog/machine-learning/qpcr-blog-post)
- K Nearest Neighbors: Simplest Machine Learning (http://andrew.gibiansky.com/blog/machine-learning/k-nearest-neighbors-simplest-machine-learning)
- Cool Linear Algebra: Singular Value Decomposition (http://andrew.gibiansky.com/blog/mathematics/cool-linear-algebra-singular-value-decomposition)
- Accelerating Options Pricing via Fourier Transforms (http://andrew.gibiansky.com/blog/economics/accelerating-options-pricing-via-fourier-transforms)
- Pricing Stock Options via the Binomial Model (http://andrew.gibiansky.com/blog/economics/binomial-options-pricing-model)
- Your Very First Microprocessor (http://andrew.gibiansky.com/blog/electrical-engineering/your-very-first-microprocessor)
- Circuits and Arithmetic (http://andrew.gibiansky.com/blog/electrical-engineering/circuits-and-arithmetic)
- Digital Design Tools: Verilog and HDLs (http://andrew.gibiansky.com/blog/electrical-engineering/digital-design-tools-verilog-and-hdls)
- Quadcopter Dynamics and Simulation (http://andrew.gibiansky.com/blog/physics/quadcopter-dynamics)
- The Digital State (http://andrew.gibiansky.com/blog/electrical-engineering/the-digital-state)
- Computing with Transistors (http://andrew.gibiansky.com/blog/electrical-engineering/computing-with-transistors)
- Machine Learning: Neural Networks (http://andrew.gibiansky.com/blog/machine-learning/machine-learning-neural-networks)
- Machine Learning: the Basics (http://andrew.gibiansky.com/blog/machine-learning/machine-learning-the-basics)
- Iranian Political Embargoes, and their Non-Existent Impact on Gasoline Prices (http://andrew.gibiansky.com/blog/economics/iranian-political-embargoes-and-their-non-existent-impact-on-gasoline-prices)
- Computational Fluid Dynamics (http://andrew.gibiansky.com/blog/physics/computational-fluid-dynamics)
- Fluid Dynamics: The Navier-Stokes Equations (http://andrew.gibiansky.com/blog/physics/fluid-dynamics-the-navier-stokes-equations)
- Image Morphing (http://andrew.gibiansky.com/blog/image-processing/image-morphing)

The content on this blog is licensed under the CC-BY-SA license (https://creativecommons.org/licenses/by-sa/2.0/).

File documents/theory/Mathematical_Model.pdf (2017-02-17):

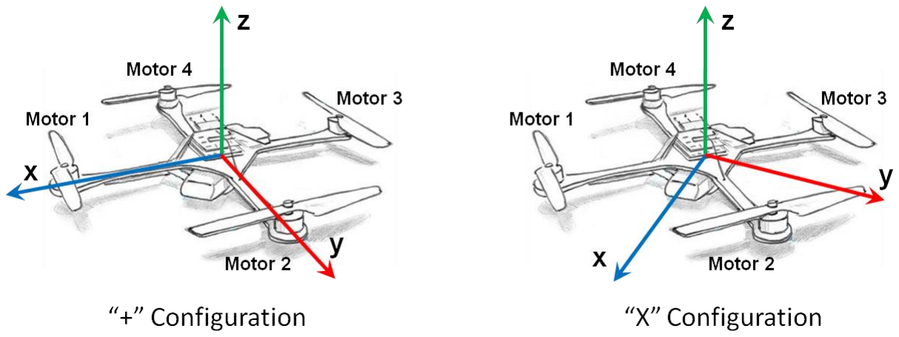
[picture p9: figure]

Mathematical Model | 1

## Mathematical Model:

Introduction

Before jumping into the mathematic model, some discussion of notation is needed.

Due to the complexity of a system with 6 degrees of freedom, various methods of notation

have been developed and are required in order to sufficiently describe the critical

variables. Shown below is an example of the notation we have chosen:

Here, the base variable is linear acceleration, or . As you can see, the variable also has two

superscripts and one subscript to further delineate what we are describing. The top left

superscript, b, tells us that the derivative taken was performed in the body frame of

reference, while the top right superscript, , tells us that the acceleration is given in terms

of body frame vector components, and the subscript, , tells us that this variable is

referencing the center of mass with respect to the inertial frame.

Another important aspect of the math model is the coordinate system that is used.

The chosen model and conventions will become very important as you work through your

model, so be sure to keep your decisions in mind and clearly documented. The coordinate

system will vary whether you use a plus (“+”) or “X” configuration, which will be described

below:

Figure 1. Plus Configuration Diagram

As seen in Fig. 1, the plus configuration we use is defined as having the X axis lie along the

arm of motor 1 (which spins counter-clockwise from above, by our convention) with the Y

axis set along the arm of motor 2 (spinning in the opposite direction of the adjacent

motors) and the Z axis pointing upward. The value represents the distance from a given

motor to the axis of rotation, and should be the same for every motor. This value will

change if using an x configuration, which is defined as a rotation in the X-Y plane of 45

degrees in the positive yaw direction, which results in having the X axis lie between motor

1 and 2. In either configuration the x axis is assumed to be the positive forward direction

for vehicle movement. For clarity, our rotation conventions are shown below in Figure 2.

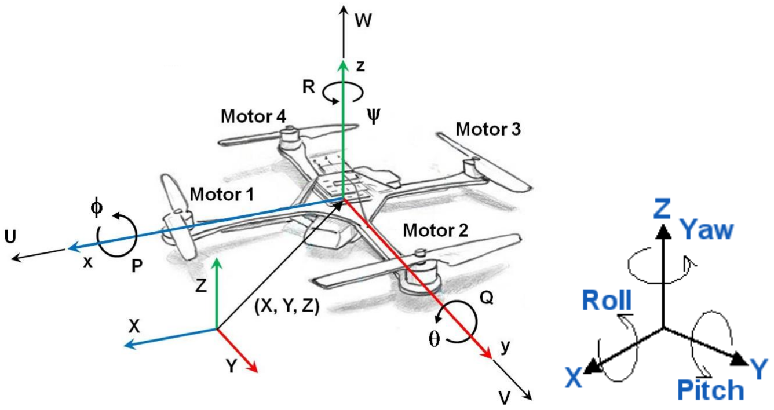
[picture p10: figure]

Figure 2. Axis labels and conventions (arrow direction positive (right-hand rotation))

Mass Moment of Inertia Matrix

One element of the system of importance is the inertia matrix. The inertia matrix

describes the quadcopters mass moment of inertia across the defined axes, and is

important to the flight dynamics of the system. With some approximations, you can

determine the mass moment of inertia across the X, Y, and Z axes in order to populate the

required inertia matrix. This particular process is covered in more detail in the Mass

Moment of Inertia documentation. Once determined using either the “+” or “X”

configuration, the inertia matrix will appear as follows:

(Mass Moment of Inertia Matrix)

Here,

is the inertia of the quadcopter relative to the body frame with | , | , and

being the inertia of the quadcopter across each axis. Due to the symmetry of the system, the

matrix is diagonal and will be identical for either a “+” or “X” configuration. The diagonal

form of the matrix is convenient due to the need to invert the matrix for use in the angular

velocity state equation.

Thrust Coefficient

The motors' thrust is the driving force behind all quadcopter maneuvers and thus is

integral to control design and simulation. The thrust, , provided by a single motor/prop

system can be calculated as follows:

Where is the thrust coefficient for a specific rotor, is the density of air,

is the cross

sectional area of the propeller's rotation, is the radius of the rotor, and is the angular

velocity of the rotor. For simple flight modeling a lumped parameter approach can be used

to simplify the characterization process:

(Thrust Coefficient Relation)

Here is the lumped parameter thrust coefficient that pertains to the individual

motor/prop system. The thrust provided by the motor/prop provides a force

perpendicular to the X-Y plane of the body frame in the positive Z direction.

Torque Coefficient

In order to understand motor effect on yaw, the torque force of the motor/prop

system must also be determined, and can be done in a similar fashion to that of the thrust

tests. The related lumped parameter equation is shown below:

(Torque Coefficient Relation)

In this case, is the torque created by the motor and is the torque coefficient for the

motor/prop system. This torque provides a force that acts to yaw the system about the z-

axis.

Initial Matrix Construction

After performing a range of tests with each of the test stands, the provided data

analysis programs can help you calculate these coefficients for characterizing your system.

With this information we can create a matrix describing the thrusts and torques on the

system like that shown below:

(“+” configuration)

All of the present values have been explained thus far except for , which is simply the

distance between the motors and the respective axes of rotation, where is the arm

length from quadcopter hub center to motor/prop.
If using an x configuration, | can instead be found by | , as that would be

the value for the distance between the motor/prop and the body's axes of rotation. Thus,

experiences no change from this configuration adjustment, while the effect of will be

distributed across all four motors for both pitch and roll.

(“X” configuration)

Throttle Command Relation

An important consideration here for control purposes is that the coefficients of

thrust and torque are based on a relationship with RPM of the motors and not something

directly determined by the control system (such as throttle command). Due to this, a linear

regression is needed that will translate throttle command values (as percent throttle) to

RPM values. The following regression was created for this purpose:

Here | is the expected steady-state motor RPM, | is the throttle percentage
command, | is the throttle % to RPM conversion coefficient, and is the y-intercept of the

linear regression relationship. The linear regression can be performed using the provided data analysis program, which allows your controller to use the proper coefficients as

determined by your motor testing for maximum accuracy and realism.

Gyroscopic Forces

There is one more set of forces to account for before we create our moment matrix,

and those are the forces resulting from gyroscopic precession. Gyroscopic precession is a

phenomenon that occurs when the axis of rotation of a rotating body is changed, and the

results are typically non-intuitive to those unfamiliar with its effects. The gyroscopic forces

resulting on the body are governed by the inertia of each motor’s rotating components

( ), the rolling and pitching rates ( and ), as well as the speed of each motor/prop system (

). The gyroscopic torques created by the motors for pitch and roll action are

shown below:

The π/30 term corresponds to the transition from RPM to radians that must occur for the

gyroscopic force to be calculated.

Final Matrix Construction

With these motor/prop forces added in to the appropriate terms we can again

organize the equations in matrix form for our simulation purposes. The resulting matrix

will account for the mentioned aerodynamic, gyroscopic, and thrust moments created by

the motor/prop systems on the quadcopter for a "+" configuration:

Here,

refers to the moments present in the body frame resulting from the

aerodynamics, thrusts, and torques on the system. The quadcopter body also experiences

forces that act on it from gravity and the lift of the rotors. The lift force can be expressed as

follows:

refers to the forces acting in the body frame on the quadcopter due to aerodynamics

and thrust (assumed oriented strictly in the positive z direction). It should be noted that

while we say there are acting aerodynamic forces, it is assumed that the static thrust and

torque tests capture the elements of aerodynamics that we are interested in. Additional

effects (such as blade flapping, frame aerodynamic drag, etc.) could be added to the model

after additional research and testing.

State Equations

Now we move on to the state equations that define the dynamics model. The first

we’ll discuss is the Angular Velocity State Equation.

(Angular Velocity State Equation)

This equation describes the change in roll ( ), pitch ( ), and yaw ( ) rates of the

quadcopter by taking into account the inertia, angular velocity, and the moments applied

by the motor/prop systems.

is the angular acceleration across each axis in the body

frame with respect to the inertial frame, and can also be written as.

Having already the inertia matrix and moment matrices, we move on to

which is a

cross-product matrix for rotational velocity. The form of this matrix is shown below:

Here, P, Q, and R are again the rotation rates about the X, Y, and Z axis, respectively. The

term is the rotational velocity of the quadcopter body within the body frame and is

defined directly by P, Q, and R.

The next state equation defined is the Euler Kinematic Equation, which allows us to

determine the rate of change of the Euler angles in the inertial frame.

Before discussing this equation we’ll discuss rotation matrices. According to the aerospace

rotation sequence, the rotation of an aircraft is described as a rotation about the z-axis

(yaw) then a rotation about the y-axis (pitch) followed by a rotation about the x-axis (roll).

Each rotation is made based on a right-handed system and in a single plane.

Using these three rotations a composite rotation matrix can be created which can

transform the motion of the aircraft from the body frame to a new reference frame. The

resulting rotation matrix transforms rotations from the body frame with respect to the

inertial frame and can be found using matrix multiplication. Below s, c, and t represent sine,

cosine, and tangent functions respectively.

Following through with the matrix multiplication yields the rotation matrix from the

inertial to the body frame using the aerospace rotation sequence:

(ZYX Sequence Rotation Matrix)

This rotation matrix is of particular importance in solving the velocity and position

state equations. A complete discussion of rotation matrices is beyond the scope of this

document.

Using sequential rotation matrices, the angular velocity of the aircraft in the body

frame can be related to the changes in angle rotation as shown below, where the C matrices

of | are those from ub.

Performing matrix multiplication and addition and taking the derivative the Euler

Kinematic Equation can be found (details not given here):

(Euler Kinematic Equation)

While this approach is effective, there is one very important drawback; a singularity

occurs when θ is equal to ± . Due to this, the accuracy and numerical stability of a

simulation can be compromised if the aircraft's pitch approaches or reaches ±90°.

Considering the modest control design intentions of this simulation, this will not be an

issue for most users. However, several approaches to avoiding this problem exist, including

using quaternions for the simulation, and thus motivated users may choose to modify our

simulation to utilize this or another approach to removing this singularity.

The next state equation we discuss is the Velocity State Equation, which describes

the acceleration of the center of mass of the rigid body quadcopter model based on the

forces and accelerations acting on the body.

(Velocity State Equation)

Here,

is the linear acceleration of the center of mass in the body frame with respect

to the inertial frame. The variable is the total mass of the quadcopter, while

is the

acceleration of gravity translated to act in the body frame by the rotation matrix

Using this equations you can find the linear acceleration of the quadcopter in the X, Y, and Z

directions of the body frame.

Finally, the last state equation to be covered is the Position State Equation, which

describes the linear velocity of the center of mass of the quadcopter in the inertial frame.

(Position State Equation)

Here,

is simply the velocity of the quadcopter in the body frame that is rotated into

the inertial frame using the transpose of

, which is

. This state equation allows us to

determine the velocity of the quadcopter in the X, Y, and Z directions of the inertial frame.

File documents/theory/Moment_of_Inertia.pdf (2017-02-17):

Mass Moment of Inertia | 1

## Mass Moment of Inertia

The mass moment of inertia of an object ( ) plays a similar role in rotational motion

as the role that mass plays in translational motion: the mass moment of inertia determines

how rotational velocity is affected by applied torque. This of course depends not only on

the mass of the object, but also on how the mass is distributed around the rotation axis.

Translational Motion Rotational Motion

We need to find the moment of inertia matrix for the quadcopter vehicle. We will use “J” for

mass moment of inertia, though various sources use different conventions for this. It is

important to note here that the quadcopter vehicle is assumed to be perfectly symmetric

about the x, y, and z axis and to have its center of mass at the geometric center of the arms.

With these assumptions, the

matrix (shown below) becomes a diagonal matrix (note that

this relates to our choice of x and y axis positions, but is preserved in both “+” and “X”
configurations). The | and | terms are also taken to be identical due to this symmetry.

The matrix is:

Approach
- Break the quadcopter vehicle into separate components. Model each of these as a

simplified geometric shape of constant internal density.

- Measure and weigh each component.
- Utilize the parallel-axis theorem to determine the moment of inertia contribution of

each component about the x, y, and z axes of the vehicle.

- Sum the inertias for every component about each axis to find the total moment of

inertia matrix for the vehicle

We utilized the parallel-axis theorem in order to determine the mass moment of inertia

of individual components our chosen axes, given an individual component’s mass moment of inertia about a parallel axis through the center of mass of that component and the

perpendicular distance between the two axes. The parallel-axis equation is:

is the moment of inertia of an individual component about its own axis (which passes

through the components center of mass) parallel to the axis we wish to “move” it to. In the

equation above, is the mass of the component, and is the perpendicular distance

between the parallel axes. Note that sign of r is not important since the value is squared.

Motors: solid cylinders (Jx,M, Jy,M, and Jz,M)

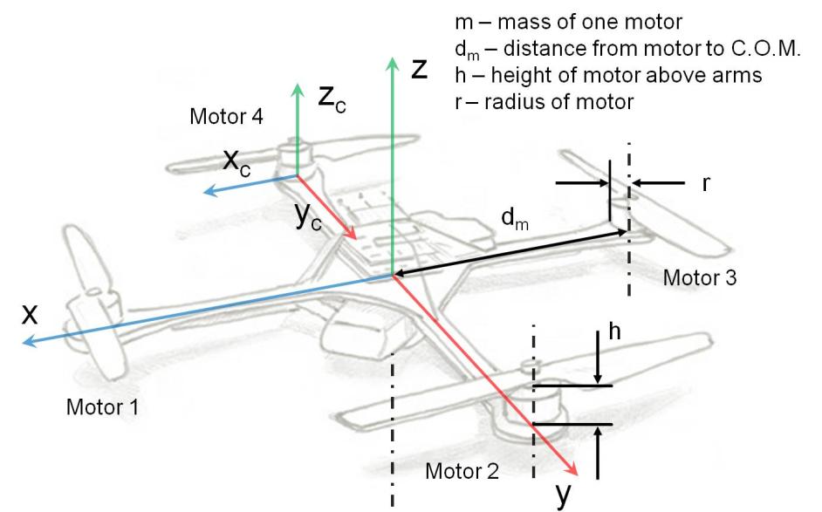
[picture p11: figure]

Equations Needed:

Cylinder rotating around an end diameter | Cylinder rotating around a central axis
X and Y axes | Z axis

and

To find | and | we use the equation for a cylinder rotating around an end diameter
(see figure above). Say we are looking to find | , for example. The first bracketed term in

the equation is for motors 1 and 3, which are rotating around an end diameter coinciding

with the x-axis of the quadcopter, therefore the distance term (

– parallel axis theorem)

is zero and is omitted. The second bracketed term in the equation is for motors 2 and 4,

which are at a diameter that is offset but parallel to the x-axis of the quad. We have a

distance term at the end here (

– except we use dm instead of r for clarity). This is the

perpendicular distance between the rotation axis of the motor and the actual x-axis of the
quad. Because of the symmetry of the vehicle, | is going to be the same value as | .
To find | we use the equation for a cylinder rotating around a central axis (see Figure above).

In this case all 4 motors are rotating around a central axis that is offset but parallel to the z-axis

of the quad. We have a distance term at the end here as well,

| , which is the

perpendicular distance between the rotation axis of the motor and the actual z-axis of the

quad. The distance term, dm, will be the same value for all 4 motors, hence incorporating all the

motors into just the 1 equation and multiplying the entire bracketed term by 4.

ESC’s: thin flat plates (Jx,S, Jy,S, and Jz,S)

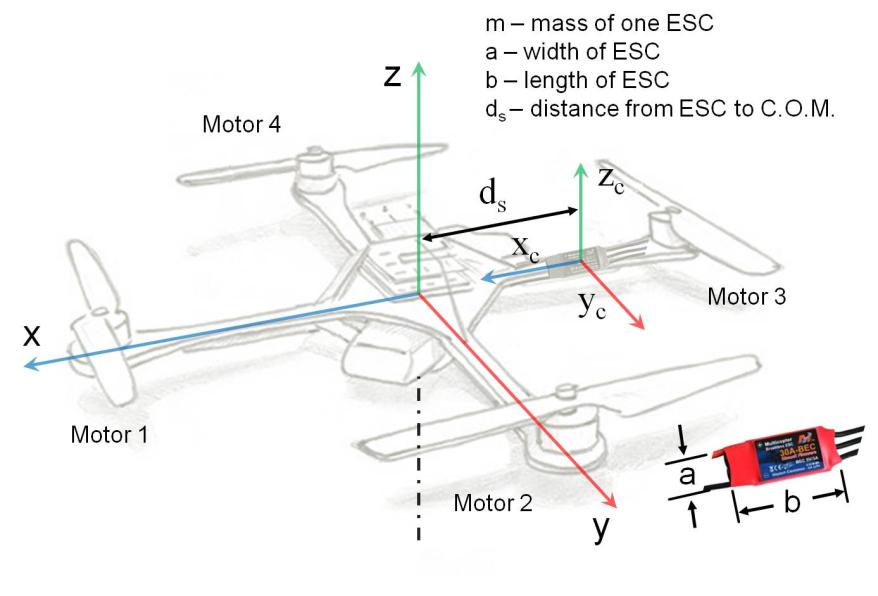
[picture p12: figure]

Equations Needed:

Flat plate rotating around X, Y, and Z axes

and

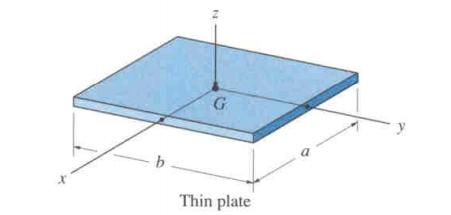
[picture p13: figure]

To find | and | we chose to use the equations for a flat plate rotating around the x and y

axes (see figure above). Suppose we are looking to find

| | for example. The first bracketed

term in the equation is for ESC’s 1 and 3 (#’s correspond to which motor they are

connected with), which are rotating around an axis coinciding with the x-axis of the quad,

therefore the distance term (

| | – parallel axis theorem) is zero. The second bracketed

term in the equation is for ESC’s 2 and 4, which are rotating around an axis that is offset but

parallel to the x-axis of the quad. We have a distance term at the end here (

| | – except we

use

instead of r). This is the perpendicular distance between the rotation axis of the ESC and the actual x-axis of the quad. Because of the symmetry of the vehicle, Jy,S is going to be

the same value as

To find Jz,S we use the equation for a flat plate rotating around the z-axis (see Figure above).

In this case all 4 ESCs are rotating around an axis that is offset but parallel to the z-axis of

the quad. We have a distance term at the end here as well,

, which is the perpendicular

distance between the rotation axis of the ESC and the actual z-axis of the quad. The distance

term,

, will be the same value for all 4 ESCs.

Central HUB: solid cylinder (Jx,H, Jy,H, Jz,H)

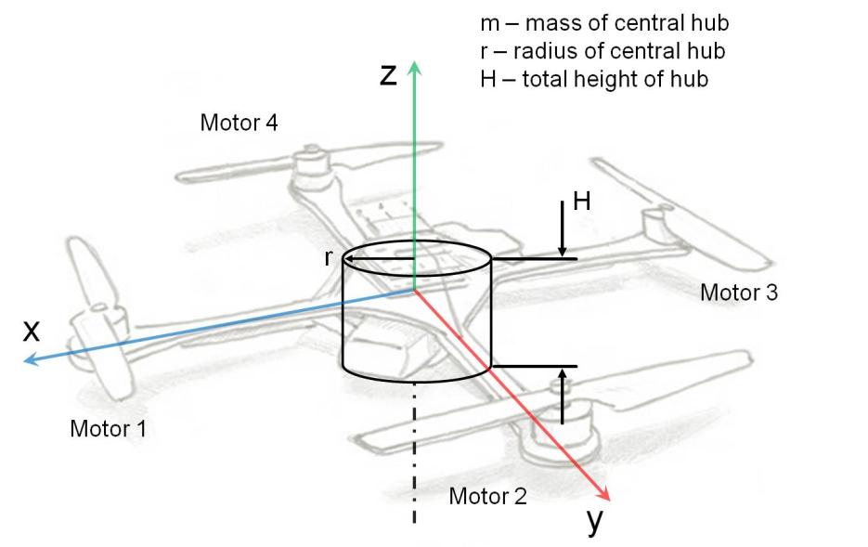
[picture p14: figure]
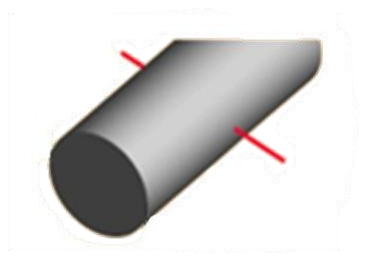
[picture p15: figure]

Equations Needed:

Cylinder rotating around a central

diameter

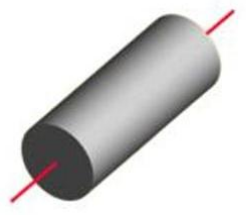
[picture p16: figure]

Cylinder rotating around a central axis

X and Y axes | Z axis

and

To find | and | we use the equation for a cylinder rotating around a central diameter
(see figure above). Say we are looking to find | , for example. The entire bracketed term

is for the central HUB, which is rotating around a central diameter coinciding with the x-

axis of the quad, therefore the distance term (

– parallel axis theorem) is zero. Because
of the symmetry of the vehicle, | is going to be the same value as | .

To find we use the equation for a cylinder rotating around a central axis (see Figure

above). In this case the hub is rotating around a central axis that coincides with the z-axis of

the quad, therefore the distance term is zero.

Arms: long cylindrical rods (Jx,A, Jy,A, Jz,A)

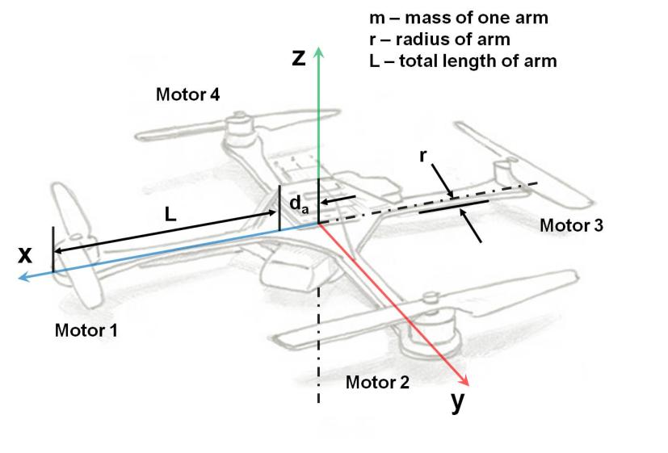
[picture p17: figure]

Equations Needed:

Cylinder rotating around a central axis | Cylinder rotating around an end diameter
X and Y axes | X, Y, and Z axes

and

To find | and | we use the equations for a cylinder rotating around a central axis, and
also an end diameter (see figure above). Say we are looking to find | , for example. The

first bracketed term in the equation is for arms 1 and 3, which are rotating around a central

axis coinciding with the x-axis of the quad, therefore the distance term (

| | – parallel axis

theorem) is zero. The second bracketed term in the equation is for arms 2 and 4 which are

rotating around an end diameter located at a distance “ ” from the x-axis of the vehicle, so

the parallel axis theorem term here is

. Because of the symmetry of the vehicle, | is
assumed to be the same as | .

To find Jz,A we use the equation for a cylinder rotating around an end diameter (see Figure

above). In this case all 4 arms are rotating around an end diameter located at a distance

“ ” from the z-axis of the vehicle, so the parallel axis theorem term is

. Also, because

the quad is symmetrical and each arm has the same length we multiply the entire

bracketed term by 4.

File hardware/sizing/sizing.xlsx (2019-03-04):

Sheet: Résumé
https://www.ecalc.ch/xcoptercalc.php?ecalc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
Hélices
Hélice - Diametre | https://hobbyking.com/fr_fr/1045-glass-fiber-nylon-black.html | inches | 9.4
Helice - Pas |  | inches | 4.3
coeff poussée |  | g/rpm^2 | 1.012523425e-05
coeff conso |  | W/rmp^3 | 1.789398541e-10
Moteur
Moteur - kv |  |  | 920
Moteur - masse |  | g | 53
Moteur - coeff a (courant vide) |  |  | 0.487
Moteur - coeff b |  |  | 0.0048
Moteur - coeff c |  |  | 1.17e-05
Batterie
Tension par cellule |  | V | 3.7
Masse |  | g | 325
Capacité |  | mAh | 5200
Cellules |  | - | 3
Résistance interne |  | ohm | 0.11
Pourcentage décharge |  | - | 90.00%
Tension |  | V | 11.1
Structure
Moteur | https://hobbyking.com/fr_fr/multistar-elite-2216-920kv-multirotor-motor-cw.html | grammes | 53
Batterie | https://hobbyking.com/fr_fr/zippy-compact-5800mah-3s-25c-lipo-pack.html | grammes | 345
ESC |  | grammes | 0
Hélice |  | grammes | 17
Masse propulsion |  | grammes | 625
Plaque Moteur | https://hobbyking.com/fr_fr/hobbykingtm-s600-s700-carbon-and-metal-quad-hexacopter-carbon-fiber-motor-mount-2pcs.html | grammes | 13
Support Moteur | https://hobbyking.com/fr_fr/hobbykingtm-s600-s700-carbon-and-metal-quad-hexacopter-motor-mount-holder-set-purple.html | grammes | 14
Bras | https://hobbyking.com/fr_fr/hobbykingtm-s600-carbon-and-metal-quadcopter-carbon-boom.html | grammes | 21
Support bras | https://hobbyking.com/fr_fr/hobbykingtm-s600-s700-carbon-and-metal-quad-hexacopter-boom-holder.html | grammes | 24
Plaques |  | grammes | 100
PCB |  | grammes | 0
Masse structure |  | grammes | 388
Support caméra |  | grammes | 340
Caméra |  | grammes | 70
Avec caméra |  |  | 0
Masse camera |  | grammes | 410
Masse totale |  | grammes | 1013
Vol stationnaire
poussée nécessaire |  | g | 1013
poussée par moteur |  | g | 253.25
vitesse rotation |  | rpm | 5001.176562
courant par moteur |  | A | 2.45
courant total |  | A | 9.8
Puissance consommée |  | W | 108.9
Puissance utilisée |  | W | 89.5
Rendement |  | % | 82.21%
Autonomie |  | min | 28.6

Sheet: Multistar Elite 2212 920 KV - 3
 |  | 9443
Régression |  | Poussée | Courant | Commande | 0.487
Moteur - kv | 920 | 139 | 1.32 | 25 | 0.0048
Moteur - masse | 53 | 313 | 3.29 | 50 | 1.17e-05
Moteur - coeff a (courant vide) | 0.487 | 526 | 6.13 | 75
Moteur - coeff b | 0.0048 | 789 | 11.6 | 100
Moteur - coeff c | 1.17e-05
Hélice - diametre | 9.4
Hélice - pas | 4.3
 |  | 1045
 |  | Poussée | Courant | Commande | 0.302
 |  | 155 | 1.36 | 25 | 0.00536
 |  | 390 | 4.1 | 50 | 1.07e-05
 |  | 694 | 9.12 | 75
 |  | 990 | 16.14 | 100

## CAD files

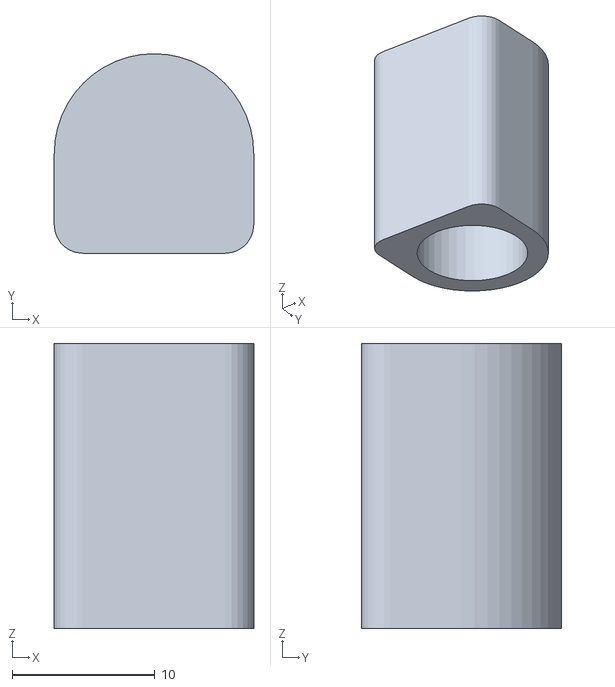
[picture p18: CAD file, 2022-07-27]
hardware/3D/quadcopter/landing_foot.stl
14.0 x 14.0 x 20.0

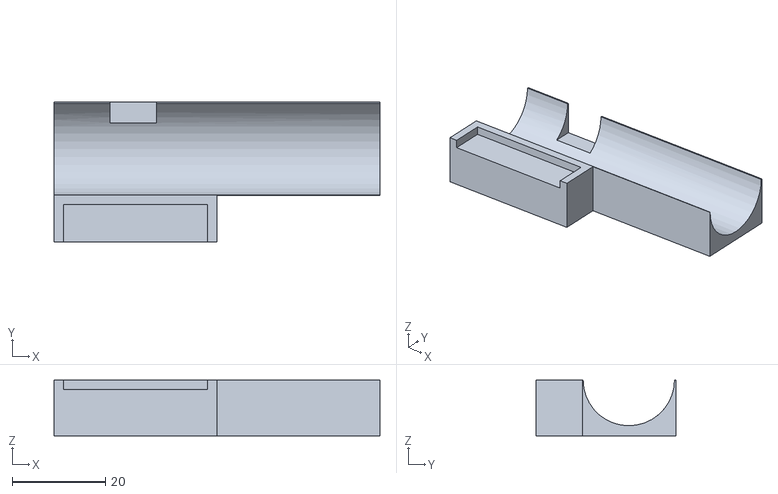
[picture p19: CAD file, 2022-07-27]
hardware/3D/remote/battery_hub_support.stl
70.0 x 30.0 x 12.0

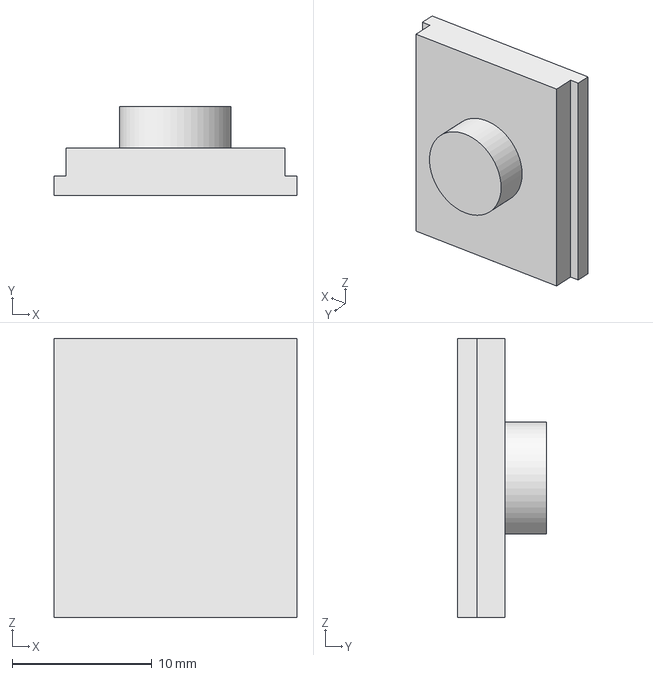
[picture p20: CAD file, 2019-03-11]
hardware/3D/test_bench/test_bench_pod_locker.fcstd
17.4 x 6.40 x 20.0 mm

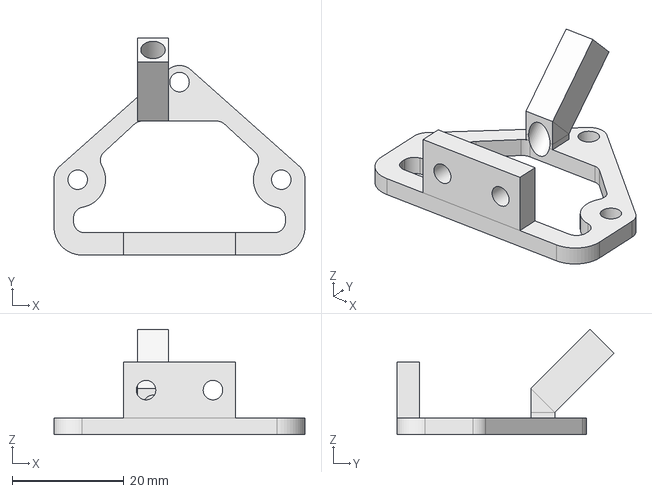
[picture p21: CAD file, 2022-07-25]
hardware/3D/quadcopter/vtx.fcstd
45.0 x 38.9 x 18.9 mm

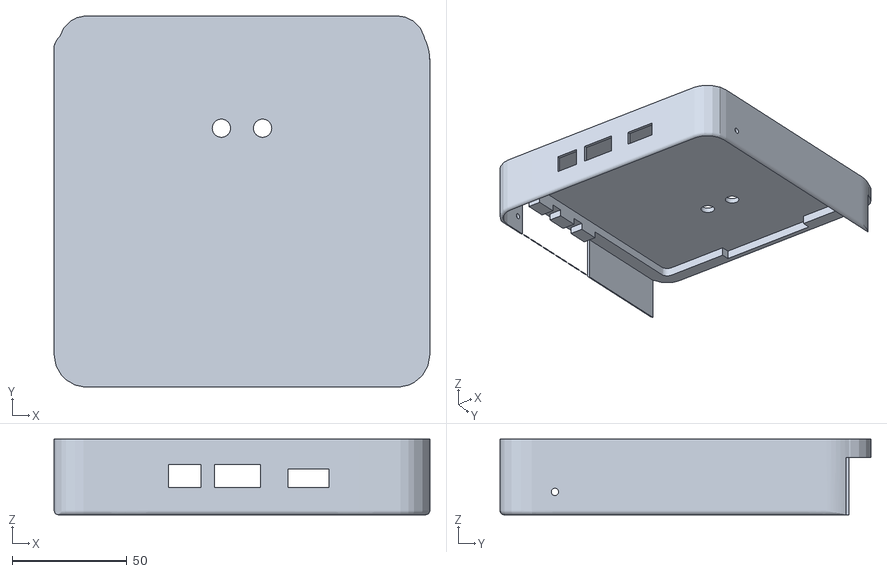
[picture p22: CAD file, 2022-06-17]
hardware/3D/remote/remote_back.stl
164.0 x 162.0 x 33.0

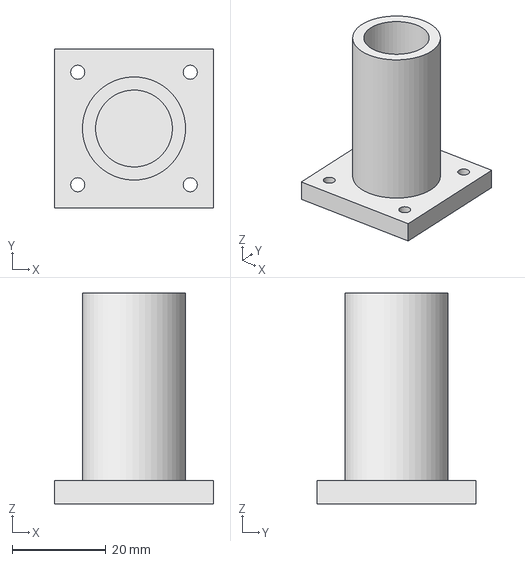
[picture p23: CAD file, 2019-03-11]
hardware/3D/test_bench/test_bench_pod_yaw.fcstd
34.0 x 34.0 x 45.0 mm

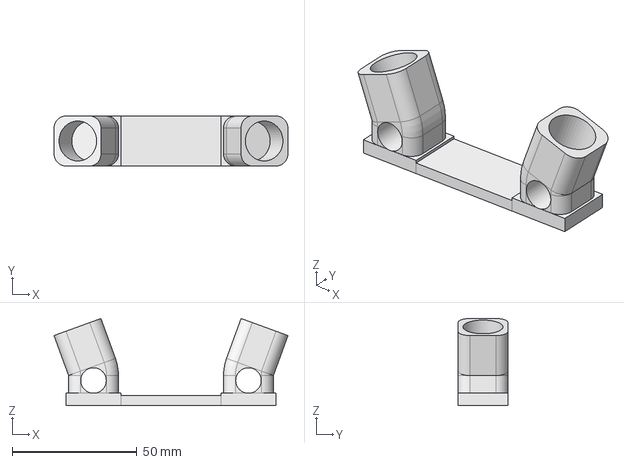
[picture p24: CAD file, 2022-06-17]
hardware/3D/quadcopter/landing_leg_holder.fcstd
93.6 x 20.2 x 34.8 mm

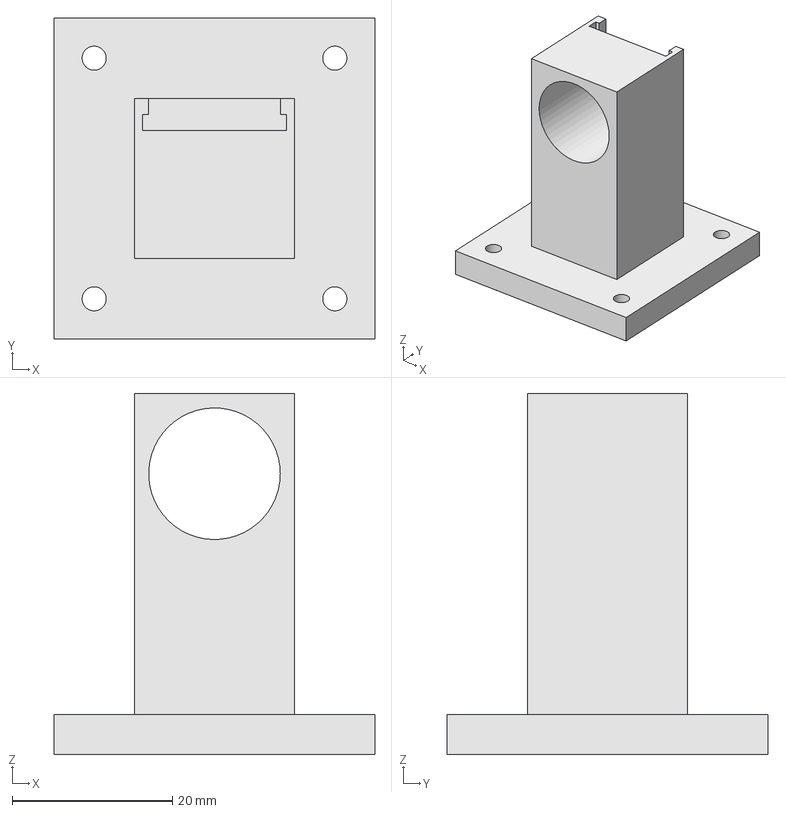
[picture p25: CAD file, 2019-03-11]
hardware/3D/test_bench/test_bench_pod.fcstd
40.0 x 40.0 x 45.0 mm

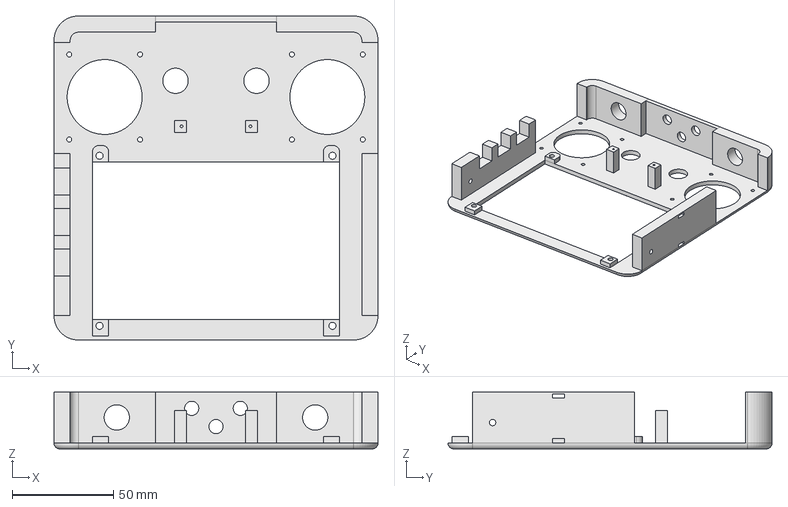
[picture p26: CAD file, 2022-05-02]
hardware/3D/remote/remote_front.fcstd
160.0 x 160.0 x 28.0 mm

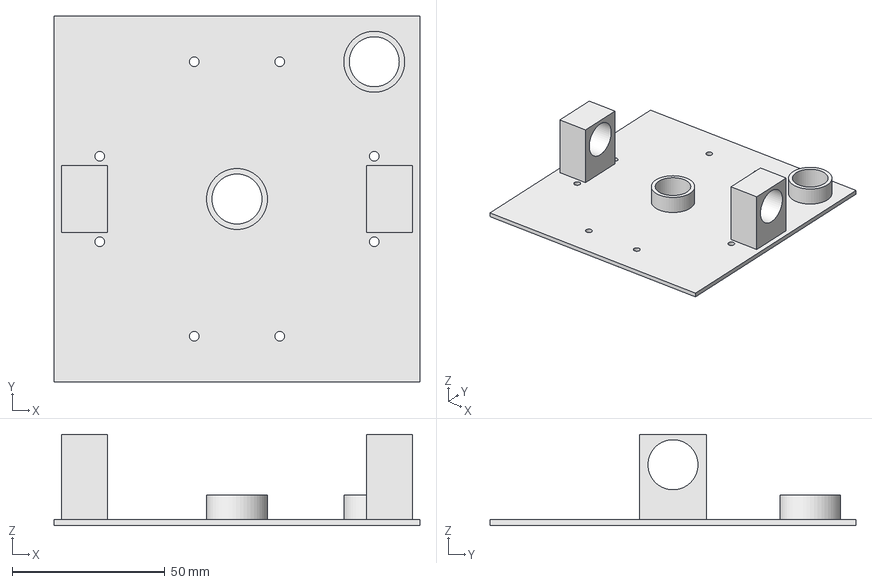
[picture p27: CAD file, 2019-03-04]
hardware/3D/test_bench/test_bench_quadcopter_plate.fcstd
120.0 x 120.0 x 30.0 mm

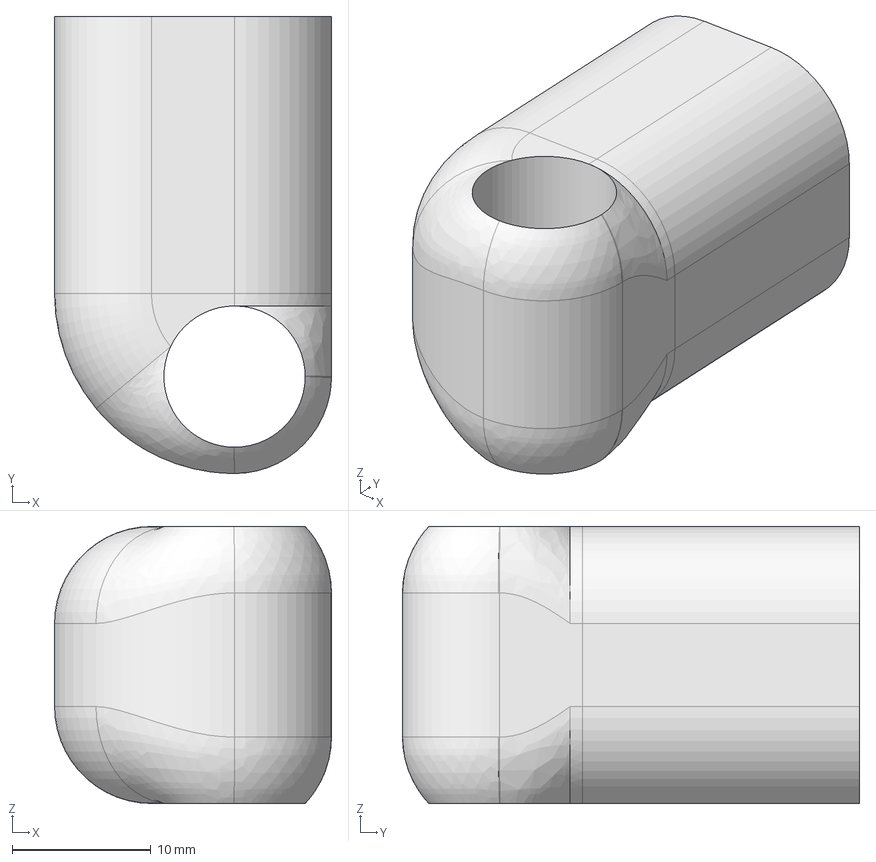
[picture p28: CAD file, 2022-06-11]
hardware/3D/quadcopter/landing_leg_T.fcstd
20.0 x 33.0 x 20.0 mm

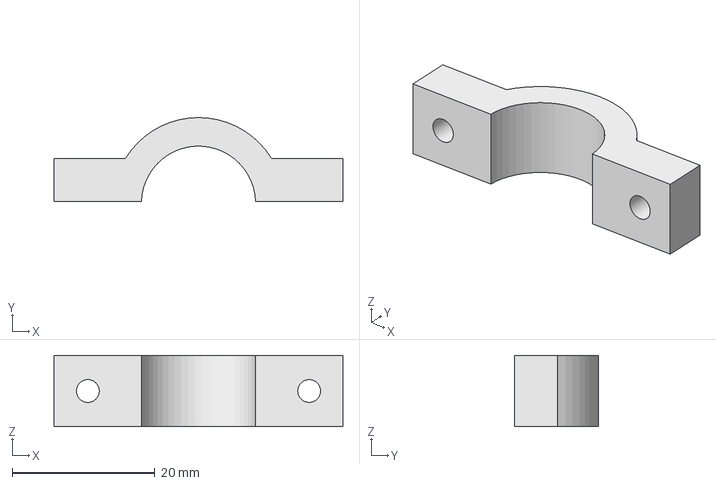
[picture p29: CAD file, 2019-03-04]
hardware/3D/test_bench/test_bench_clip.fcstd
40.5 x 11.8 x 10.0 mm

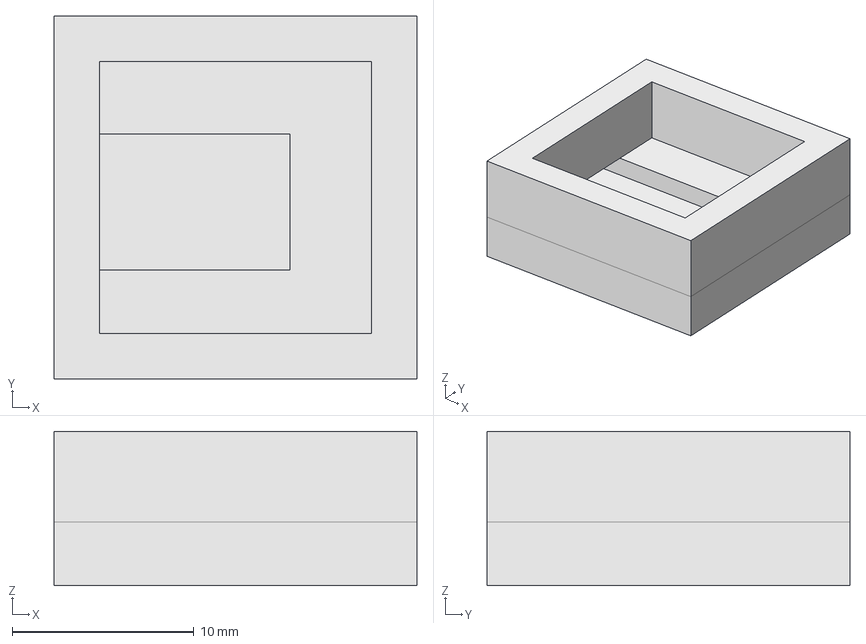
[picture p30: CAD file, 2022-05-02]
hardware/3D/quadcopter/gps_antenna_holder.fcstd
20.0 x 20.0 x 8.50 mm

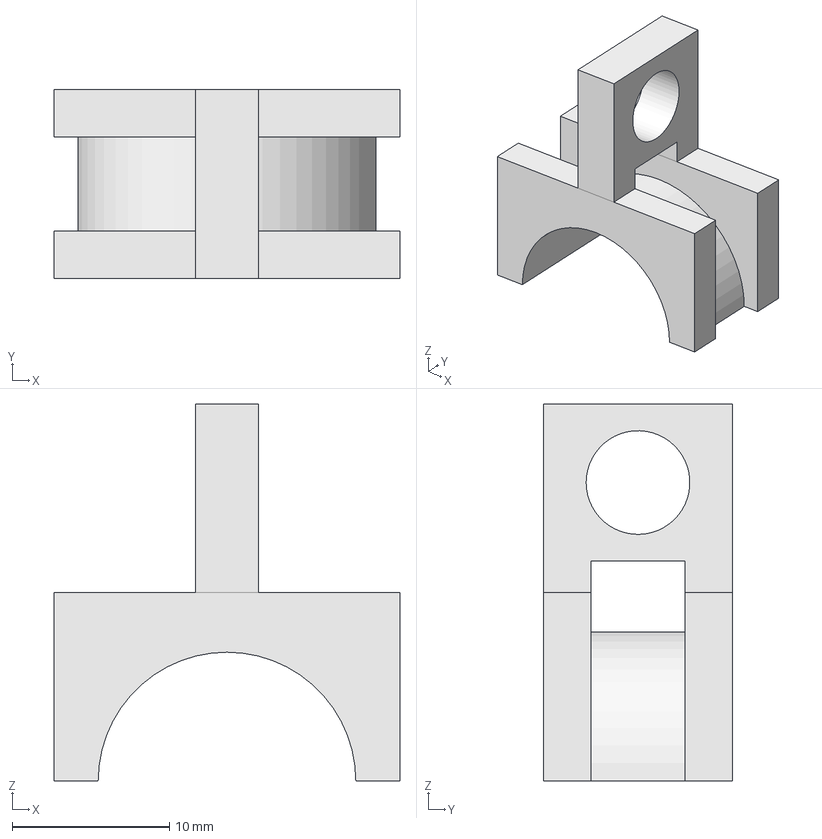
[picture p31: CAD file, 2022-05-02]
hardware/3D/quadcopter/rf_antenna_holder.fcstd
22.0 x 12.0 x 24.0 mm

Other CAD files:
hardware/3D/remote/hub_battery_support.fcstd
hardware/3D/quadcopter/land_foot.fcstd
hardware/3D/quadcopter/rf_board_holder.fcstd
hardware/3D/quadcopter/gimbal_rail_holder_blind_ultrasound.FCStd
hardware/3D/quadcopter/gimbal_rail_holder_blind.FCStd
hardware/3D/quadcopter/gimbal_rail_holder_blind.stl
hardware/3D/quadcopter/gimbal_rail_holder_blind_battery.FCStd
hardware/3D/quadcopter/gimbal_rail_holder_blind_battery.stl
hardware/3D/quadcopter/gimbal_rail_holder_blind_ultrasound.stl
hardware/3D/quadcopter/gimbal_rail_holder_through.FCStd
hardware/3D/quadcopter/gimbal_rail_holder_through.stl
hardware/3D/quadcopter/gps_antenna_holder.stl
hardware/3D/quadcopter/landing_leg_T.stl
hardware/3D/quadcopter/landing_leg_holder.stl
hardware/3D/quadcopter/rf_antenna_holder.stl
hardware/3D/quadcopter/rf_board_holder.stl
hardware/3D/quadcopter/side.FCStd
hardware/3D/quadcopter/side.stl
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

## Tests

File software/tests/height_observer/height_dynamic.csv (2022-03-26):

sensors.ultrasound.height | sensors.barometer.height | sensors.accelerometer.vertical | control.attitude.height.position.current | control.attitude.height.speed.current
0 | 0.253104 | 0.0422586 | 0.401245 | 0.0854049
0 | 0.253104 | 0.0271651 | 0.401442 | 0.0854546
0 | 0.160474 | 0.02269 | 0.401221 | 0.0853847
0 | 0.139335 | 0.0509388 | 0.400125 | 0.0868638
0 | 0.164022 | 0.0451765 | 0.399953 | 0.0873466
0 | 0.123553 | 0.0354781 | 0.401023 | 0.0917386
0 | 0.180021 | 0.0391396 | 0.401 | 0.0920491
0 | 0.435039 | 0.0337059 | 0.409343 | 0.0949342
0 | 0.469464 | 0.0279027 | 0.410541 | 0.0949826
0 | 0.543451 | 0.025325 | 0.413524 | 0.0949367
0 | 0.509026 | 0.0185036 | 0.414862 | 0.0947576
0 | 0.472938 | 0.041625 | 0.41852 | 0.0954859
0 | 0.522312 | 0.0361994 | 0.419888 | 0.0957462
0 | 0.522312 | 0.0243722 | 0.421252 | 0.0957116
0 | 0.511817 | 0.030055 | 0.422566 | 0.0958179
0 | 0.517933 | 0.0239666 | 0.434005 | 0.0976633
0 | 0.517933 | 0.0306009 | 0.435289 | 0.0977778
0 | 0.505626 | 0.0438239 | 0.436519 | 0.0982191
0 | 0.533862 | 0.0367056 | 0.439082 | 0.0988526
0 | 0.549791 | 0.0289888 | 0.440473 | 0.0989242
0 | 0.549791 | 0.0158873 | 0.441858 | 0.0986705
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

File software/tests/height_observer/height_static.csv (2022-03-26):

sensors.ultrasound.height | sensors.barometer.height | sensors.accelerometer.vertical | control.attitude.height.position.current | control.attitude.height.speed.current
0 | 0.370825 | 0.0211702 | 0.742906 | 0.142909
0 | 0.32947 | 0.0296189 | 0.743518 | 0.143329
0 | 0.321524 | 0.0152326 | 0.744079 | 0.143384
0 | 0.321524 | 0.0210416 | 0.744645 | 0.143269
0 | 0.240652 | 0.0157482 | 0.74511 | 0.143278
0 | 0.240652 | 0.0183236 | 0.74511 | 0.143352
0 | 0.173836 | 0.0110182 | 0.744644 | 0.143195
0 | 0.169349 | 0.00685762 | 0.744152 | 0.142932
0 | 0.253681 | 0.0205623 | 0.743386 | 0.143098
0 | 0.253681 | 0.0241747 | 0.743523 | 0.143338
0 | 0.337202 | 0.0230793 | 0.744254 | 0.143612
0 | 0.337202 | 0.00488427 | 0.744985 | 0.143432
0 | 0.364501 | 0.0169979 | 0.746874 | 0.14335
0 | 0.364501 | 0.00740356 | 0.747786 | 0.143254
0 | 0.267736 | 0.00722353 | 0.748023 | 0.143084
0 | 0.240437 | 0.0202701 | 0.748076 | 0.143221
0 | 0.240437 | 0.0288988 | 0.748141 | 0.143575
0 | 0.244112 | 0.0260498 | 0.748244 | 0.143861
0 | 0.288115 | 0.0254746 | 0.748662 | 0.144166
0 | 0.288115 | 0.021003 | 0.749088 | 0.144359
0 | 0.262439 | 0.0126689 | 0.753296 | 0.145491
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

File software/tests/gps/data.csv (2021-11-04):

longitude | latitude
43.535355 | 1.518987
43.535355 | 1.518984
43.535354 | 1.518987
43.535354 | 1.519985
43.535354 | 1.518987
43.535353 | 1.518989
43.535353 | 1.518997
43.535353 | 1.518998
43.535353 | 1.519006
43.535354 | 1.519009
43.535354 | 1.519013
43.535354 | 1.519017

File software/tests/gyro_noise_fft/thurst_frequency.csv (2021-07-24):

thurst | frequency
0.10 | 15.5
0.15 | 23.2
0.20 | 61.0
0.25 | 74.8
0.30 | 88.0
0.35 | 101.4
0.40 | 113.0
0.45 | 124.3
0.50 | 135.0

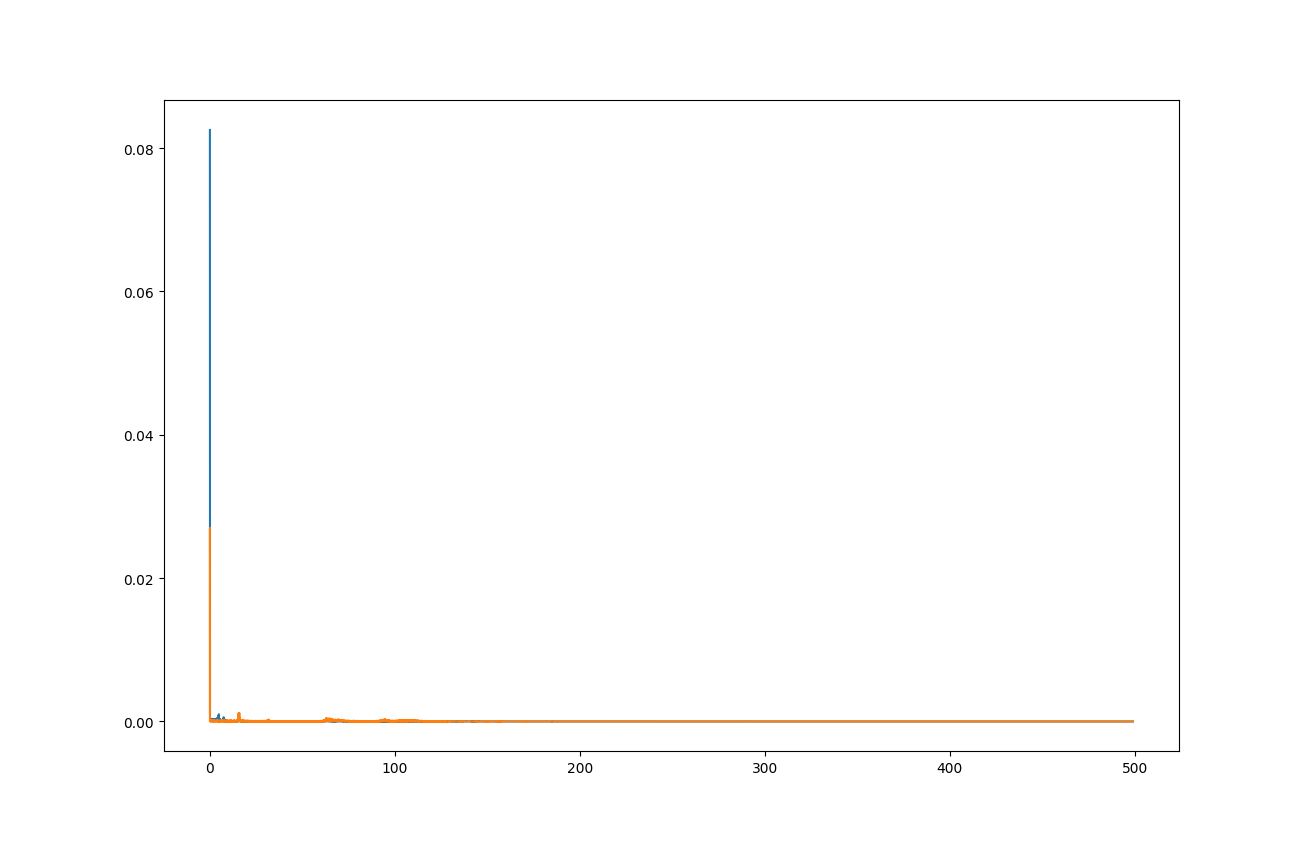
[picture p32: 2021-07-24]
software/tests/gyro_noise_fft/gyro_fft_10.png

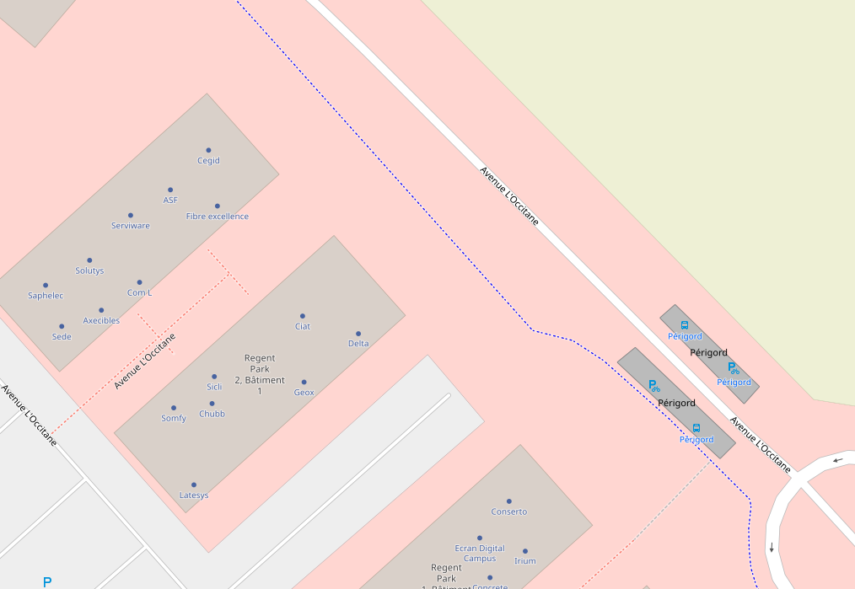
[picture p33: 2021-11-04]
software/tests/gps/map.png

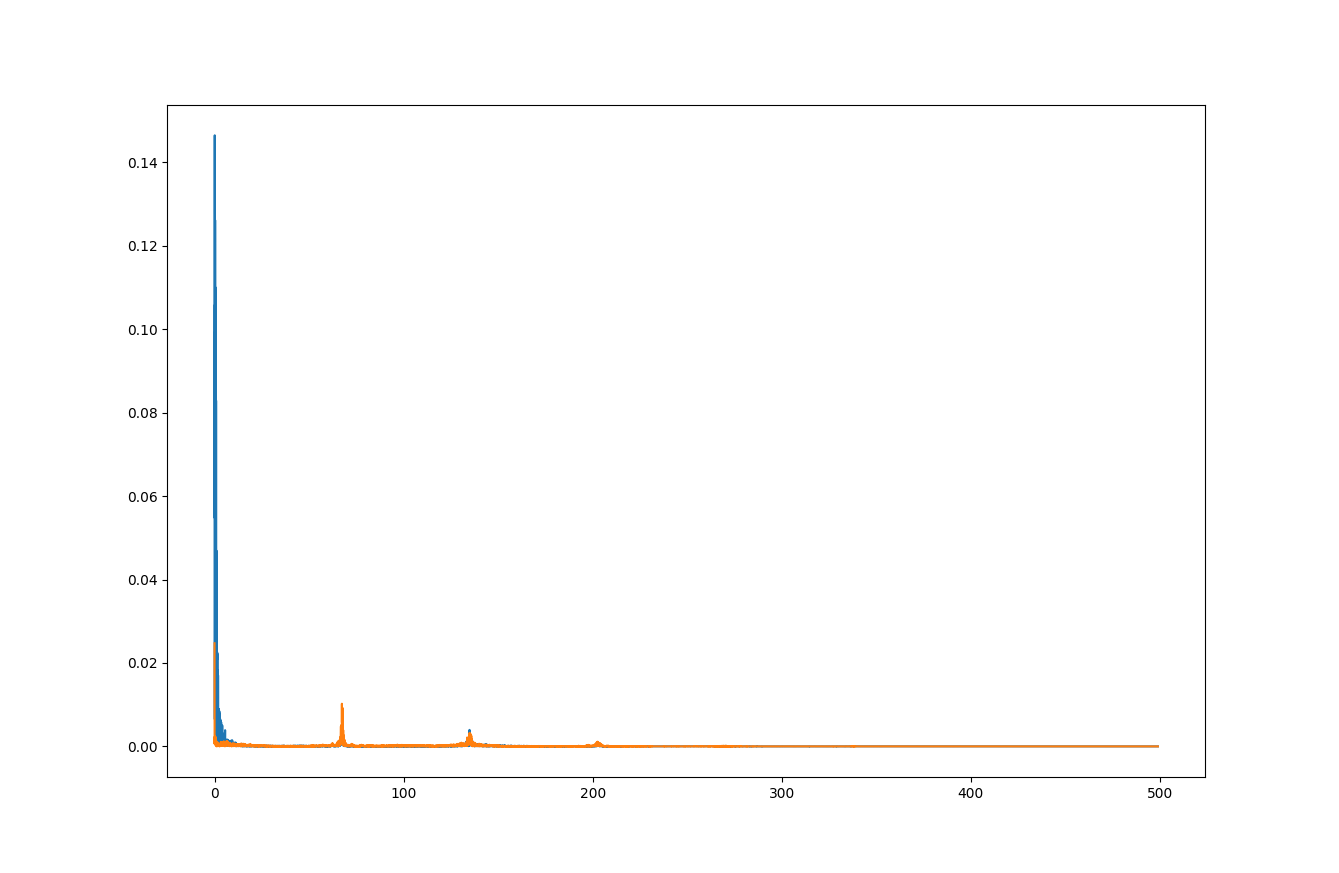
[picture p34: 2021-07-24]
software/tests/gyro_noise_fft/gyro_fft_50.png

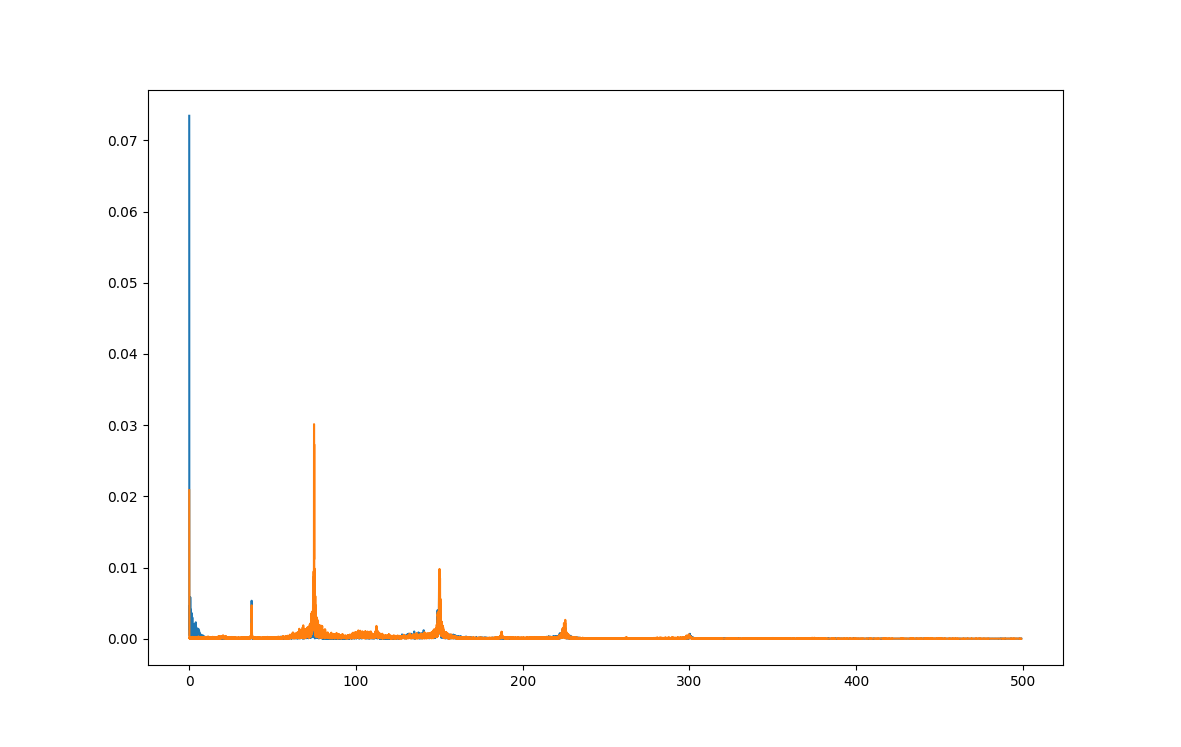
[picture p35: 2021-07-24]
software/tests/gyro_noise_fft/gyro_fft_25.png

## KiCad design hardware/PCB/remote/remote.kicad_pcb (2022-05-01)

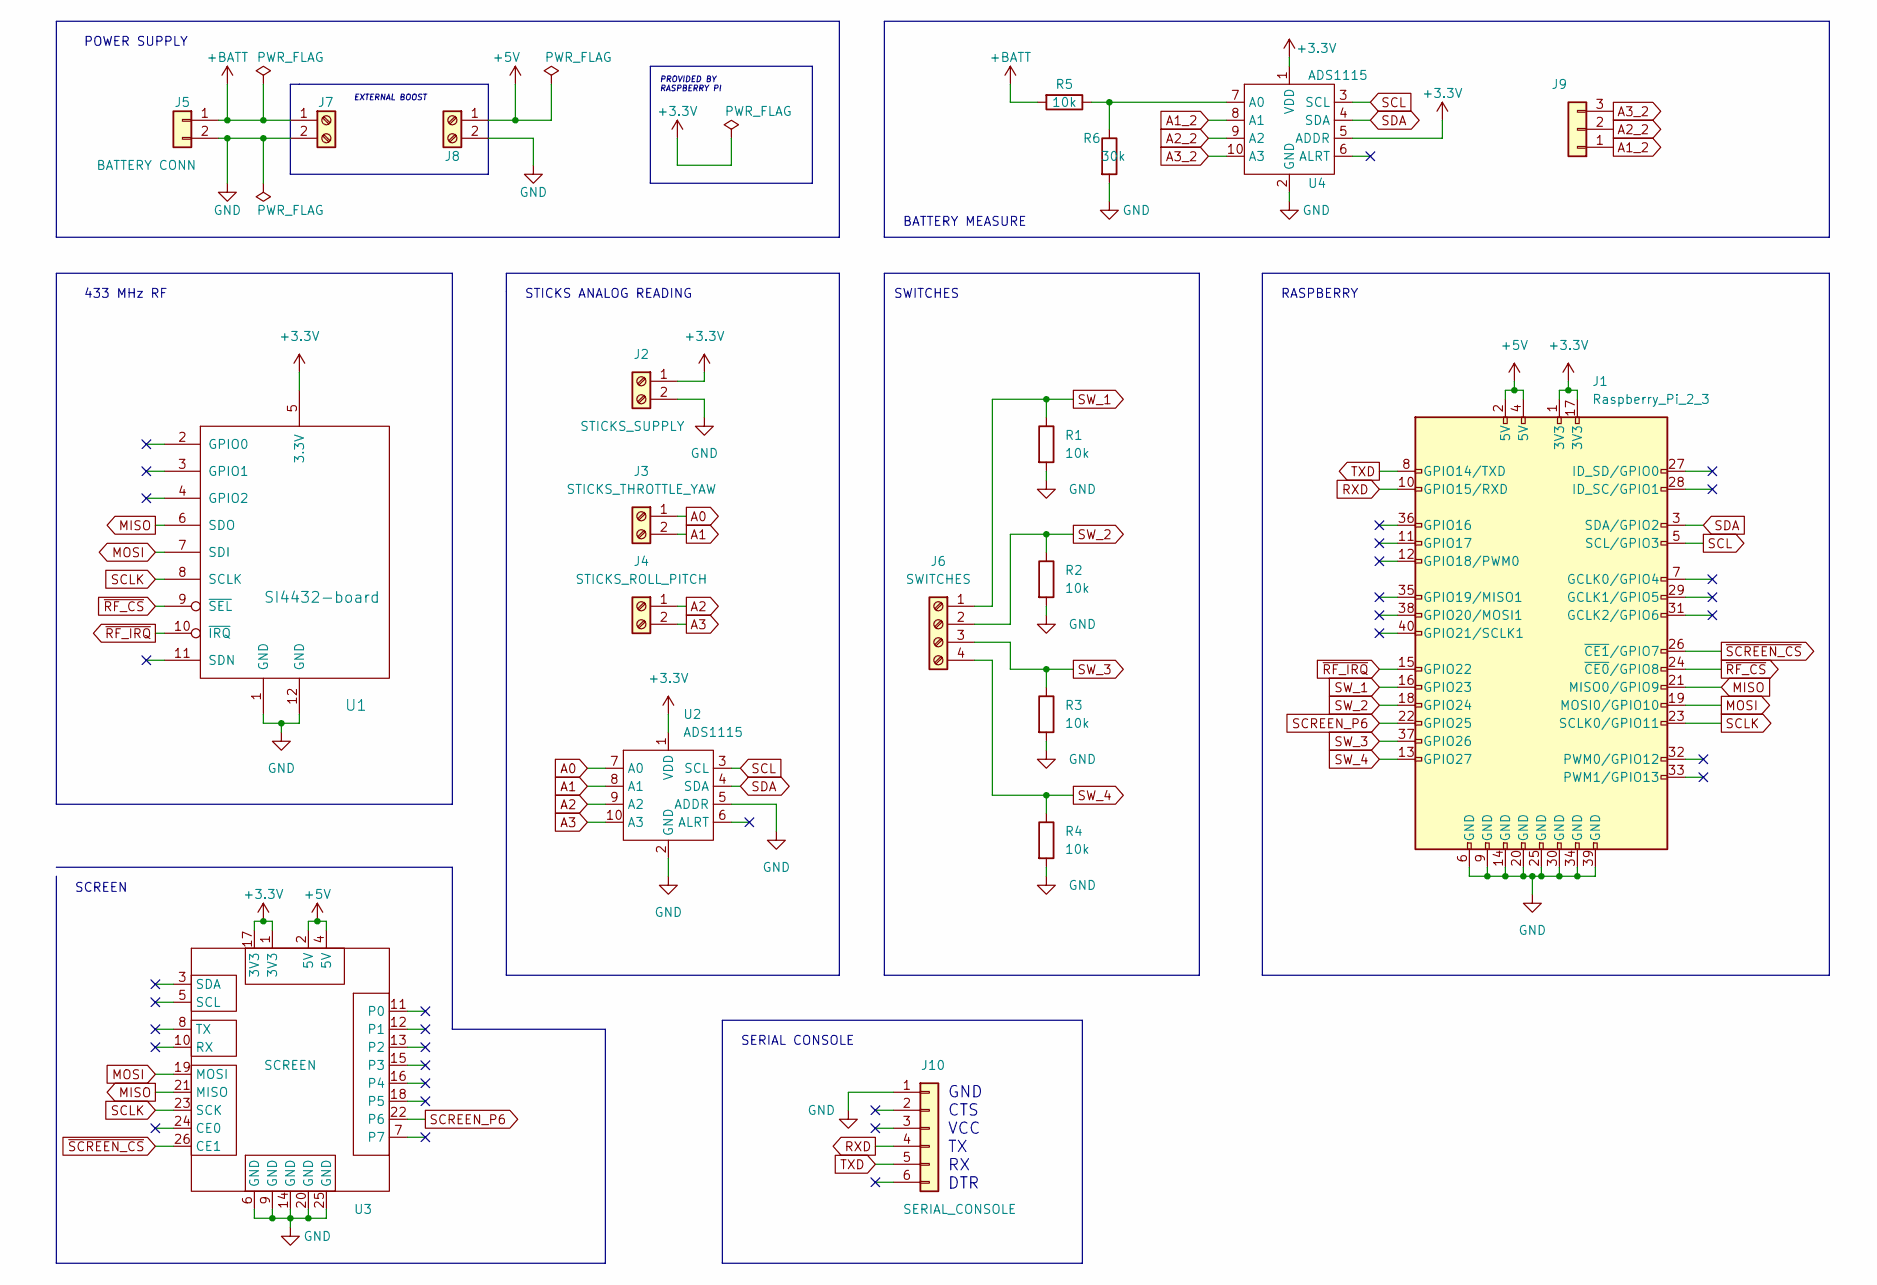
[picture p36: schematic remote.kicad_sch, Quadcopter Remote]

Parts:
J1: Raspberry_Pi_2_3; Raspberry_Pi_Zero_Socketed_THT_FaceDown_MountingHoles
J2: STICKS_SUPPLY; TerminalBlock_bornier-2_P5.08mm
J3: STICKS_THROTTLE_YAW; TerminalBlock_bornier-2_P5.08mm
J4: STICKS_ROLL_PITCH; TerminalBlock_bornier-2_P5.08mm
J5: BATTERY CONN; BATTERY_CHARGER
J6: SWITCHES; TerminalBlock_bornier-4_P5.08mm
J7, J8, J9: (no value)
J10: SERIAL_CONSOLE; PinHeader_1x06_P2.54mm_Vertical
R1, R2, R3, R4, R5: 10k; R_1206_3216Metric_Pad1.30x1.75mm_HandSolder
R6: 30k; R_1206_3216Metric_Pad1.30x1.75mm_HandSolder
U1: SI4432-board
U2, U4: ADS1115
U3: SCREEN; PinHeader_2x13_P2.54mm_Vertical

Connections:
+3V3: J1.1 (3V3), J1.17 (3V3), J2.1, U1.5 (3.3V), U2.1 (VDD), U3.1 (3V3), U3.17 (3V3), U4.1 (VDD), U4.5 (ADDR)
+5V: J1.2 (5V), J1.4 (5V), J8.1, U3.2 (5V), U3.4 (5V)
+BATT: J5.1, J7.1, R5.2
A0: J3.1, U2.7 (A0)
A1: J3.2, U2.8 (A1)
A1_2: J9.1, U4.8 (A1)
A2: J4.1, U2.9 (A2)
A2_2: J9.2, U4.9 (A2)
A3: J4.2, U2.10 (A3)
A3_2: J9.3, U4.10 (A3)
GND: J1.6 (GND), J1.9 (GND), J1.14 (GND), J1.20 (GND), J1.25 (GND), J1.30 (GND), J1.34 (GND), J1.39 (GND), J2.2, J5.2, J7.2, J8.2, J10.1, R1.2, R2.2, R3.2, R4.2, R6.2, U1.1 (GND), U1.12 (GND), U2.2 (GND), U2.5 (ADDR), U3.6 (GND), U3.9 (GND), U3.14 (GND), U3.20 (GND), U3.25 (GND), U4.2 (GND)
MISO: J1.21 (MISO0/GPIO9), U1.6 (SDO), U3.21 (MISO)
MOSI: J1.19 (MOSI0/GPIO10), U1.7 (SDI), U3.19 (MOSI)
unnamed: R5.1, R6.1, U4.7 (A0)
RXD: J1.10 (GPIO15/RXD), J10.4
SCL: J1.5 (SCL/GPIO3), U2.3 (SCL), U4.3 (SCL)
SCLK: J1.23 (SCLK0/GPIO11), U1.8 (SCLK), U3.23 (SCK)
SCREEN_P6: J1.22 (GPIO25), U3.22 (P6)
SDA: J1.3 (SDA/GPIO2), U2.4 (SDA), U4.4 (SDA)
SW_1: J1.16 (GPIO23), J6.1, R1.1
SW_2: J1.18 (GPIO24), J6.2, R2.1
SW_3: J1.37 (GPIO26), J6.3, R3.1
SW_4: J1.13 (GPIO27), J6.4, R4.1
TXD: J1.8 (GPIO14/TXD), J10.5
~RF_CS: J1.24 (~CE0/GPIO8), U1.9 (~SEL)
~RF_IRQ: J1.15 (GPIO22), U1.10 (~IRQ)
~SCREEN_CS: J1.26 (~CE1/GPIO7), U3.26 (CE1)

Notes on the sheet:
SERIAL CONSOLE
GND CTS VCC TX RX DTR
EXTERNAL BOOST
SWITCHES
BATTERY MEASURE
PROVIDED BY RASPBERRY PI
STICKS ANALOG READING
SCREEN
RASPBERRY
POWER SUPPLY
433 MHz RF

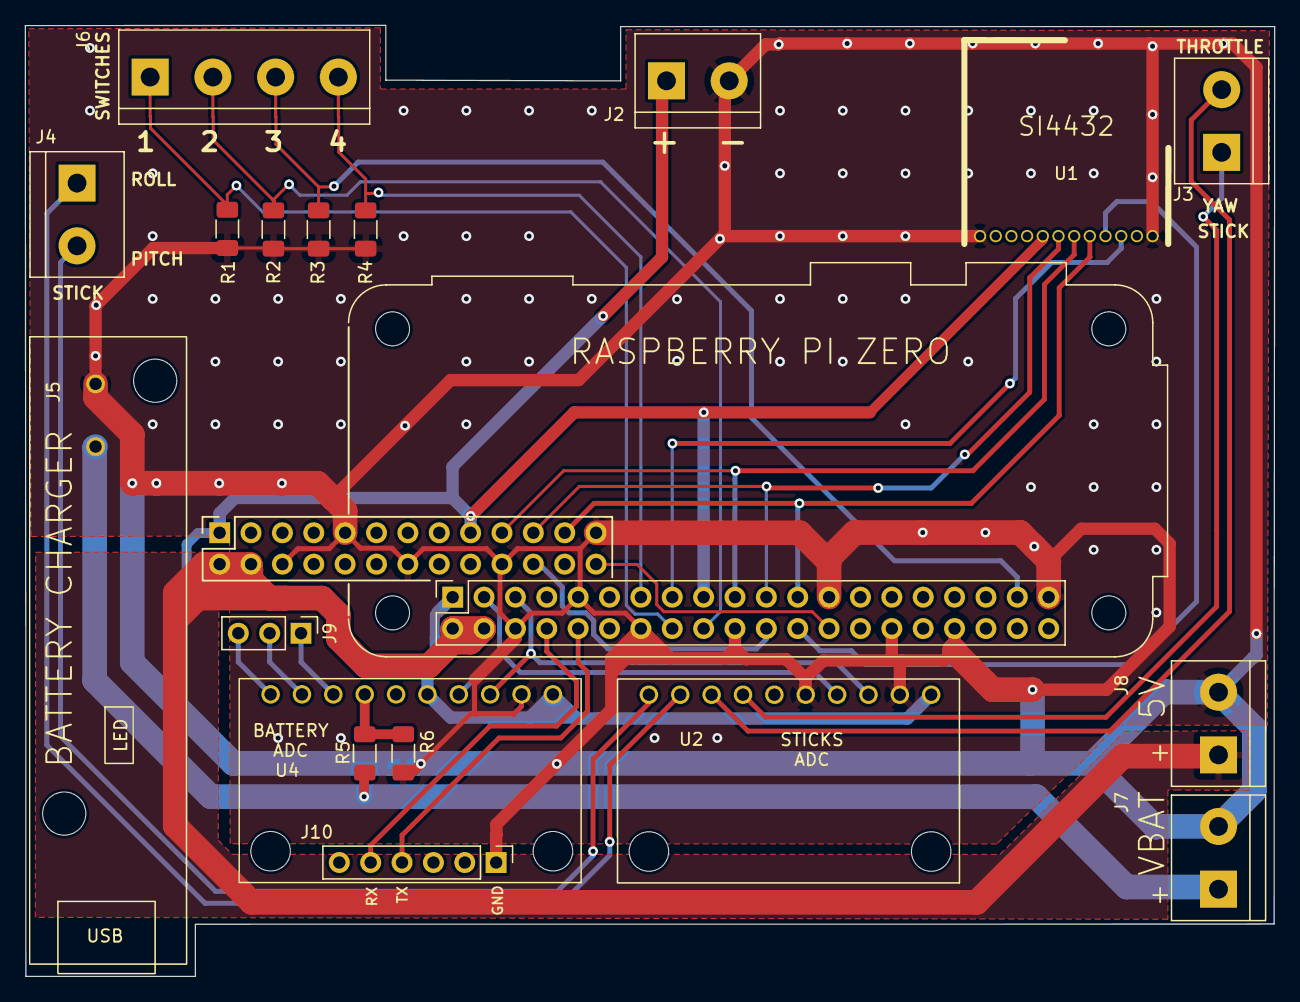
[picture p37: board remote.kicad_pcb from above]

Board: 2 copper layers, 101.2 x 77.0 mm, 20 parts (1 on the bottom side), 27 nets.

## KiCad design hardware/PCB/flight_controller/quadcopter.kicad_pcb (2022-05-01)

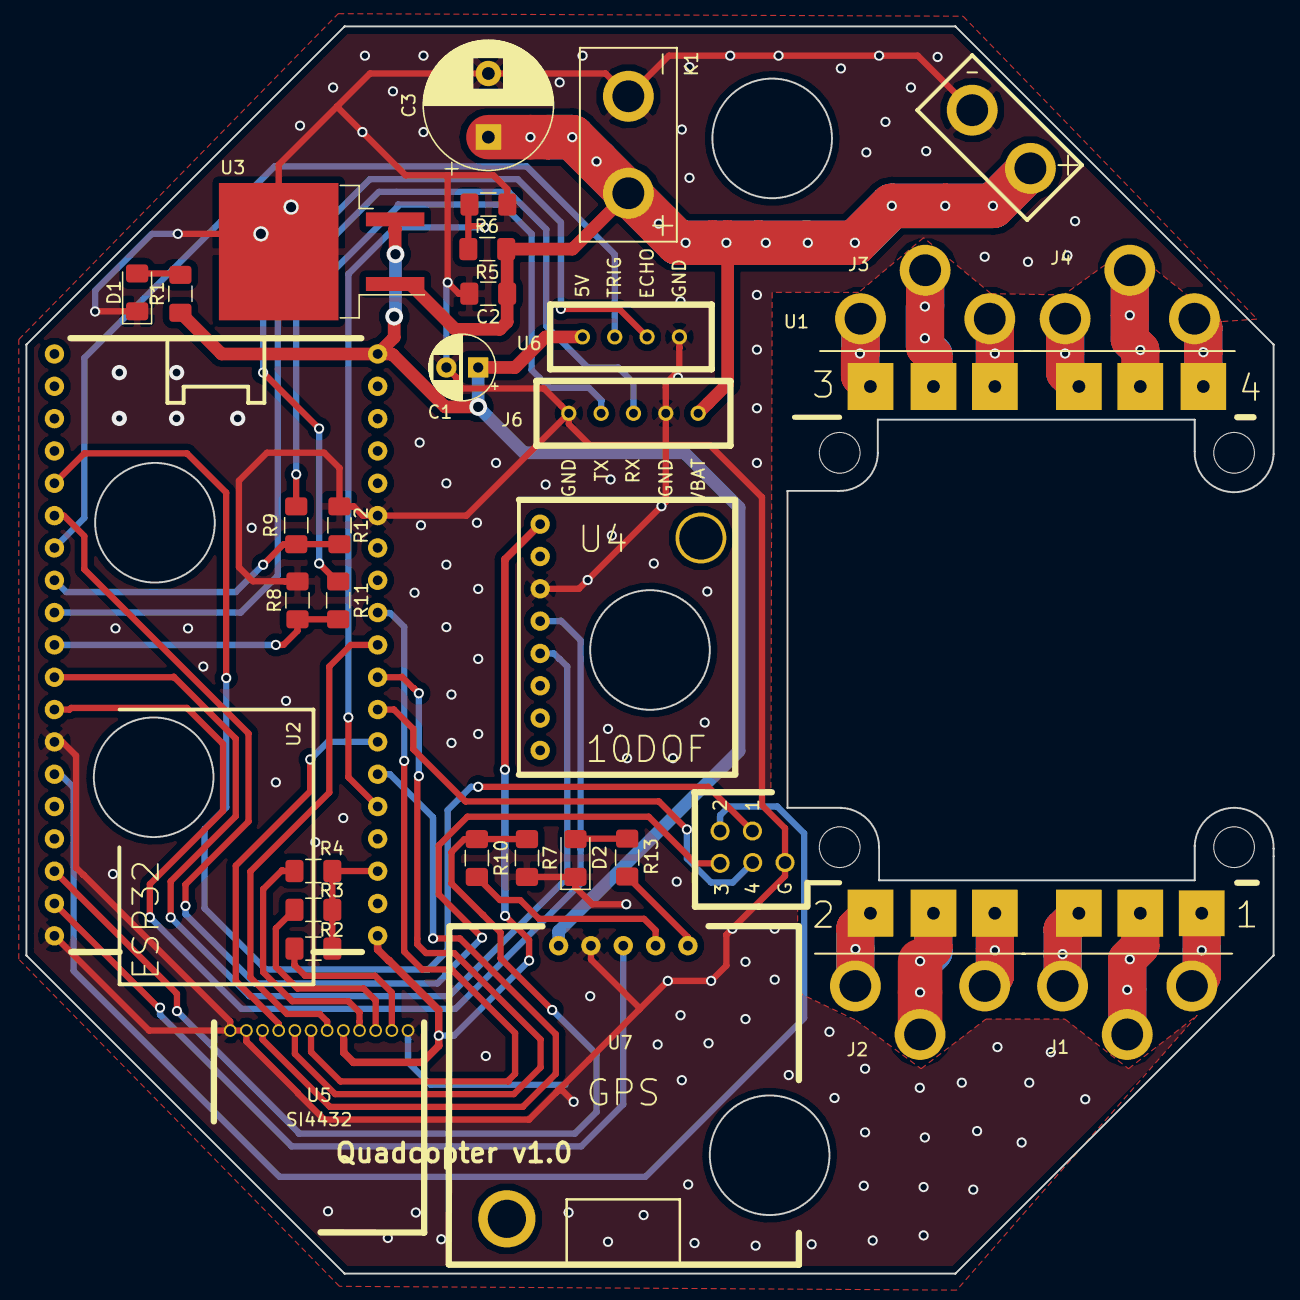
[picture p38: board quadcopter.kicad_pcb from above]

Board: 2 copper layers, 98.0 x 98.0 mm, 31 parts (0 on the bottom side), 44 nets.

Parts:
C1: 22u; CP_Radial_D5.0mm_P2.50mm
C2: 470n; C_1206_3216Metric_Pad1.42x1.75mm_HandSolder
C3: 470u; CP_Radial_D10.0mm_P5.00mm
D1, D2: LED; LED_1206_3216Metric_Pad1.42x1.75mm_HandSolder
J1, J2, J3, J4: CONN-MOTOR; motor-connector
J6: GIMBAL
K1: BATTERY; battery-connector
R1, R13: 1k; R_1206_3216Metric_Pad1.42x1.75mm_HandSolder
R2, R3, R4: 0; R_1206_3216Metric_Pad1.42x1.75mm_HandSolder
R5: 30k; R_1206_3216Metric_Pad1.42x1.75mm_HandSolder
R6, R10, R11, R12: 10k; R_1206_3216Metric_Pad1.42x1.75mm_HandSolder
R7, R8, R9: 20k; R_1206_3216Metric_Pad1.42x1.75mm_HandSolder
U1: ESC
U2: ESP-WROOM-32-board; ESP32-VROOM-board
U3: LM2936-5.0; TO-263-2
U4: 10DOF
U5: SI4432-board
U6: HC-SR04
U7: GPS

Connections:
+3V3: U2.1, U4.1, U5.5
+5V: C1.1, R1.1, U2.19, U3.3, U6.1, U7.1
+BATT: C2.1, C3.1, J6.1, K1.1, R5.1, U1.1, U3.1
ESC_CMD1: U1.16, U2.24
ESC_CMD2: U1.17, U2.33
ESC_CMD3: U1.18, U2.25
ESC_CMD4: U1.19, U2.8
GIMBAL_RX: J6.3, U2.28
GIMBAL_TX: R9.1, R12.2, U2.27
GND: C1.2, C2.2, C3.2, D1.1, D2.1, J6.2, J6.5, K1.2, R6.2, R7.2, R8.2, R9.2, U1.2, U1.15, U2.14, U2.32, U2.38, U3.2, U4.3, U5.1, U5.11, U5.12, U6.4, U7.4
GPS_RX: U2.37, U7.3
GPS_TX: R7.1, R10.2, U2.36
HC-SR04_ECHO: R8.1, R11.2, U2.29
HC-SR04_TRIG: U2.26, U6.2
MEAS_BATT: R5.2, R6.1, U2.5
unnamed: D1.2, R1.2
unnamed: D2.2, R13.2
unnamed: J1.1, U1.3
unnamed: J1.2, U1.4
unnamed: J1.3, U1.5
unnamed: J2.1, U1.6
unnamed: J2.2, U1.7
unnamed: J2.3, U1.8
unnamed: J3.1, U1.9
unnamed: J3.2, U1.10
unnamed: J3.3, U1.11
unnamed: J4.1, U1.12
unnamed: J4.2, U1.13
unnamed: J4.3, U1.14
unnamed: J6.4, R12.1
unnamed: R2.1, U5.2
unnamed: R3.1, U5.3
unnamed: R4.1, U5.4
unnamed: R10.1, U7.2
unnamed: R11.1, U6.3
unnamed: R13.1, U7.5
SCK: U2.9, U5.8
SCL: U2.31, U4.4
SDA: U2.30, U4.5
SDI: U2.11, U5.7
SDO: U2.10, U5.6
SI4432_GPIO: R2.2, R3.2, R4.2, U2.3
~SI4432_IRQ: U2.6, U5.10
~SI4432_SEL: U2.7, U5.9

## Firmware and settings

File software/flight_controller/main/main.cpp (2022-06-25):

#include <nvs_flash.h>

#include <string.h>

#include <platform.h>

#include <app/controllers/attitude_controller.h>
#include <app/controllers/height_controller.h>
#include <app/controllers/position_controller.h>
#include <app/controllers/rate_controller.h>
#include <app/controllers/motors_controller.h>

#include <app/workers/data_recorder.h>
#include <app/workers/telemetry.h>
#include <app/workers/battery_supervisor.h>
#include <app/workers/camera_controller.h>
#include <app/workers/heartbeat.h>
#include <app/workers/data_model_controller.h>
#include <app/workers/broker.h>
#include <app/workers/radio_command.h>

#include <data_model/data_ressources_registry.h>
#include <data_model/json_protocol.h>
#include <data_model/binary_protocol.h>

#include <periph/i2c_master.h>
#include <periph/uart.h>
#include <periph/spi.h>

#include <hal/gps.h>
#include <hal/log.h>
#include <hal/marg.h>
#include <hal/motor.h>
#include <hal/wifi.h>
#include <hal/radio.h>
#include <hal/radio.h>
#include <hal/camera.h>

#include <drv/SI4432.h>

#include <os/task.h>

#include <utils/mixer.h>

// #define DATA_RECORDING

extern "C" void app_main(void)
{
    Logger                  * logger;
    Motor                   * front_left;
    Motor                   * front_right;
    Motor                   * rear_left;
    Motor                   * rear_right;
    I2cMaster               * sensors_i2c;
    Marg                    * marg;
    SPIHost                 * spi;
    Si4432                  * transceiver;
#ifdef DATA_RECORDING
    DataRecorder            * data_recorder;
#else
    Mixer                   * mixer;
    RateController          * rate_controller;
    AttitudeController      * attitude_controller;
    HeightController        * height_controller;
    PositionController      * position_controller;
    Gps                     * gps;
    MotorsController        * motors_controller;
    Wifi                    * wifi;
    Radio                   * radio;
    DataRessourcesRegistry  * registry;
    JsonDataProtocol        * json_protocol;
    BinaryDataProtocol      * binary_protocol;
    BatterySupervisor       * battery_supervisor;
    Camera                  * camera;
    CameraController        * camera_controller;
    UltrasoundSensor        * ultrasound;
    Barometer               * barometer;
    Telemetry               * telemetry;
    RadioCommand            * radio_command;
    Adc                     * adc;
    Battery                 * battery;
    Heartbeat               * heartbeat;
    Broker                  * broker;
    DataModelController     * data_model_controller;
#endif

    nvs_flash_init();

    (void)logger;
    (void)position_controller;

    adc = new Adc(PLATFORM_BATTERY_ADC_UNIT);
    battery = new Battery(adc, PLATFORM_BATTERY_ADC_CHANNEL, PLATFORM_BATTERY_CELLS, PLATFORM_BATTERY_DIVIDER);

    sensors_i2c = new I2cMaster(I2C_MASTER_NUM);
    sensors_i2c->init();

    marg = new Marg(sensors_i2c);
    marg->init();

    spi = new SPIHost(PLATFORM_SPI_NUM, PLATFORM_SPI_MOSI_PIN, PLATFORM_SPI_MISO_PIN, PLATFORM_SPI_CLK_PIN, 64);
    transceiver = new Si4432(spi);

#ifndef DATA_RECORDING
    barometer = new Barometer(sensors_i2c);
    barometer->init();

    ultrasound = new UltrasoundSensor();
#endif

    front_left  = new Motor(PLATFORM_FRONT_LEFT_PULSE_CHANNEL,  PLATFORM_FRONT_LEFT_PULSE_PIN);
    front_right = new Motor(PLATFORM_FRONT_RIGHT_PULSE_CHANNEL, PLATFORM_FRONT_RIGHT_PULSE_PIN);
    rear_left   = new Motor(PLATFORM_REAR_LEFT_PULSE_CHANNEL,   PLATFORM_REAR_LEFT_PULSE_PIN);
    rear_right  = new Motor(PLATFORM_REAR_RIGHT_PULSE_CHANNEL,  PLATFORM_REAR_RIGHT_PULSE_PIN);

    front_left->arm();
    front_right->arm();
    rear_left->arm();
    rear_right->arm();

    front_left->set_speed(0.0f);
    front_right->set_speed(0.0f);
    rear_left->set_speed(0.0f);
    rear_right->set_speed(0.0f);

#ifdef DATA_RECORDING
    data_recorder         = new DataRecorder(front_left, front_right, rear_left, rear_right, marg);
#else
    registry              = new DataRessourcesRegistry("data_model.json");
    json_protocol         = new JsonDataProtocol(registry);
    binary_protocol       = new BinaryDataProtocol(registry);
    wifi                  = new Wifi();
    mixer                 = new Mixer(front_left, front_right, rear_left, rear_right);
    motors_controller     = new MotorsController(MOTORS_CONTROLLER_PERIOD, registry, mixer);
    rate_controller       = new RateController(RATE_CONTROLLER_PERIOD, marg, mixer, registry);
    attitude_controller   = new AttitudeController(ATTITUDE_CONTROLLER_PERIOD, registry, rate_controller, marg);
    height_controller     = new HeightController(HEIGHT_CONTROLLER_PERIOD, registry, marg, barometer, ultrasound, attitude_controller, rate_controller);
    position_controller   = new PositionController(POSITION_CONTROLLER_PERIOD, registry);
    gps                   = new Gps(registry, PLATFORM_GPS_UART, PLATFORM_GPS_RX_PIN, PLATFORM_GPS_TX_PIN);
    battery_supervisor    = new BatterySupervisor(BATTERY_SUPERVISOR_PERIOD, battery, registry);
    camera                = new Camera(wifi);
    camera_controller     = new CameraController(CAMERA_SUPERVISOR_PERIOD, registry, camera);
    radio                 = new Radio(transceiver);
    broker                = new Broker(BROKER_PERIOD, radio);
    logger                = new Logger(broker);
    telemetry             = new Telemetry(registry, 100, broker);
    radio_command         = new RadioCommand(registry, broker);
    heartbeat             = new Heartbeat(HEARTBEAT_PERIOD, broker, front_left);
    data_model_controller = new DataModelController(DATA_MODEL_CONTROLLER_PERIOD, broker, json_protocol, binary_protocol);

    registry->internal_set<string>("control.mode", "off");
    registry->internal_set<string>("control.phase", "landed");

#endif

    rate_controller->calibrate_gyro();

#ifdef DATA_RECORDING
    data_recorder->start();
#else

    wifi->connect();

    /* Very High */
    rate_controller->start();

    /* High */
    attitude_controller->start();
    height_controller->start();

    /* Medium */
    transceiver->start();
    broker->start();
    radio_command->start();

    /* Low */
    data_model_controller->start();
    gps->start();

    /* Very Low */
    heartbeat->start();
    telemetry->start();
    battery_supervisor->start();
    motors_controller->start();
    camera->start();
    camera_controller->start();

#endif

    while (true)
    {
        Task::delay_ms(1000);
    }
}

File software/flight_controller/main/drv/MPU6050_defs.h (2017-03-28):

#pragma once                     

#define MPU6050_ADDRESS_AD0_LOW                 (0x68) 		///< address pin low (GND), default for InvenSense evaluation board
#define MPU6050_ADDRESS_AD0_HIGH                (0x69) 		///< address pin high (VCC)

#define MPU6050_RA_XG_OFFS_TC                   (0x00) 		///< [7] PWR_MO DE, [6:1] XG_OFFS_TC, [0] OTP_BNK_VLD
#define MPU6050_RA_YG_OFFS_TC                   (0x01) 		///< [7] PWR_MODE, [6:1] YG_OFFS_TC, [0] OTP_BNK_VLD
#define MPU6050_RA_ZG_OFFS_TC                   (0x02) 		///< [7] PWR_MODE, [6:1] ZG_OFFS_TC, [0] OTP_BNK_VLD
#define MPU6050_RA_X_FINE_GAIN                  (0x03) 		///< [7:0] X_FINE_GAIN
#define MPU6050_RA_Y_FINE_GAIN                  (0x04) 		///< [7:0] Y_FINE_GAIN
#define MPU6050_RA_Z_FINE_GAIN                  (0x05) 		///< [7:0] Z_FINE_GAIN
#define MPU6050_RA_XA_OFFS_H                    (0x06) 		///< [15:0] XA_OFFS
#define MPU6050_RA_XA_OFFS_L_TC                 (0x07)
#define MPU6050_RA_YA_OFFS_H                    (0x08) 		///< [15:0] YA_OFFS    
#define MPU6050_RA_YA_OFFS_L_TC                 (0x09)
#define MPU6050_RA_ZA_OFFS_H                    (0x0A) 		///< [15:0] ZA_OFFS
#define MPU6050_RA_ZA_OFFS_L_TC                 (0x0B)
#define MPU6050_RA_SELF_TEST_X                  (0x0D) 		///< [7:5] XA_TEST[4-2], [4:0] XG_TEST[4-0]
#define MPU6050_RA_SELF_TEST_Y                  (0x0E) 		///< [7:5] YA_TEST[4-2], [4:0] YG_TEST[4-0]
#define MPU6050_RA_SELF_TEST_Z                  (0x0F) 		///< [7:5] ZA_TEST[4-2], [4:0] ZG_TEST[4-0]
#define MPU6050_RA_SELF_TEST_A                  (0x10) 		///< [5:4] XA_TEST[1-0], [3:2] YA_TEST[1-0], [1:0] ZA_TEST[1-0]
#define MPU6050_RA_XG_OFFS_USRH                 (0x13) 		///< [15:0] XG_OFFS_USR
#define MPU6050_RA_XG_OFFS_USRL                 (0x14)
#define MPU6050_RA_YG_OFFS_USRH                 (0x15) 		///< [15:0] YG_OFFS_USR
#define MPU6050_RA_YG_OFFS_USRL                 (0x16)
#define MPU6050_RA_ZG_OFFS_USRH                 (0x17) 		///< [15:0] ZG_OFFS_USR
#define MPU6050_RA_ZG_OFFS_USRL                 (0x18)
#define MPU6050_RA_SMPLRT_DIV                   (0x19)
#define MPU6050_RA_CONFIG                       (0x1A)
#define MPU6050_RA_GYRO_CONFIG                  (0x1B)
#define MPU6050_RA_ACCEL_CONFIG                 (0x1C)
#define MPU6050_RA_FF_THR                       (0x1D)
#define MPU6050_RA_FF_DUR                       (0x1E)
#define MPU6050_RA_MOT_THR                      (0x1F)
#define MPU6050_RA_MOT_DUR                      (0x20)
#define MPU6050_RA_ZRMOT_THR                    (0x21)
#define MPU6050_RA_ZRMOT_DUR                    (0x22)
#define MPU6050_RA_FIFO_EN                      (0x23)
#define MPU6050_RA_I2C_MST_CTRL                 (0x24)
#define MPU6050_RA_I2C_SLV0_ADDR                (0x25)
#define MPU6050_RA_I2C_SLV0_REG                 (0x26)
#define MPU6050_RA_I2C_SLV0_CTRL                (0x27)
#define MPU6050_RA_I2C_SLV1_ADDR                (0x28)
#define MPU6050_RA_I2C_SLV1_REG                 (0x29)
#define MPU6050_RA_I2C_SLV1_CTRL                (0x2A)
#define MPU6050_RA_I2C_SLV2_ADDR                (0x2B)
#define MPU6050_RA_I2C_SLV2_REG                 (0x2C)
#define MPU6050_RA_I2C_SLV2_CTRL                (0x2D)
#define MPU6050_RA_I2C_SLV3_ADDR                (0x2E)
#define MPU6050_RA_I2C_SLV3_REG                 (0x2F)
#define MPU6050_RA_I2C_SLV3_CTRL                (0x30)
#define MPU6050_RA_I2C_SLV4_ADDR                (0x31)
#define MPU6050_RA_I2C_SLV4_REG                 (0x32)
#define MPU6050_RA_I2C_SLV4_DO                  (0x33)
#define MPU6050_RA_I2C_SLV4_CTRL                (0x34)
#define MPU6050_RA_I2C_SLV4_DI                  (0x35)
#define MPU6050_RA_I2C_MST_STATUS               (0x36)
#define MPU6050_RA_INT_PIN_CFG                  (0x37)
#define MPU6050_RA_INT_ENABLE                   (0x38)
#define MPU6050_RA_DMP_INT_STATUS               (0x39)
#define MPU6050_RA_INT_STATUS                   (0x3A)
#define MPU6050_RA_ACCEL_XOUT_H                 (0x3B)
#define MPU6050_RA_ACCEL_XOUT_L                 (0x3C)
#define MPU6050_RA_ACCEL_YOUT_H                 (0x3D)
#define MPU6050_RA_ACCEL_YOUT_L                 (0x3E)
#define MPU6050_RA_ACCEL_ZOUT_H                 (0x3F)
#define MPU6050_RA_ACCEL_ZOUT_L                 (0x40)
#define MPU6050_RA_TEMP_OUT_H                   (0x41)
#define MPU6050_RA_TEMP_OUT_L                   (0x42)
#define MPU6050_RA_GYRO_XOUT_H                  (0x43)
#define MPU6050_RA_GYRO_XOUT_L                  (0x44)
#define MPU6050_RA_GYRO_YOUT_H                  (0x45)
#define MPU6050_RA_GYRO_YOUT_L                  (0x46)
#define MPU6050_RA_GYRO_ZOUT_H                  (0x47)
#define MPU6050_RA_GYRO_ZOUT_L                  (0x48)
#define MPU6050_RA_EXT_SENS_DATA_00             (0x49)
#define MPU6050_RA_EXT_SENS_DATA_01             (0x4A)
#define MPU6050_RA_EXT_SENS_DATA_02             (0x4B)
#define MPU6050_RA_EXT_SENS_DATA_03             (0x4C)
#define MPU6050_RA_EXT_SENS_DATA_04             (0x4D)
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

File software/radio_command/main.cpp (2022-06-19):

#include <iostream>
#include <platform.hpp>
#include <periph/i2c.hpp>
#include <drv/ADS1115.hpp>
#include <app/video_feedback.hpp>
#include <app/radio_command.hpp>
#include <app/battery_monitor.hpp>

int main(int argc, char ** argv)
{
    I2C            i2c     = I2C(PLATFORM_BATTERY_I2C);
    ADS1115        ads     = ADS1115(&i2c);
    BatteryMonitor battery = BatteryMonitor(&ads, PLATFORM_BATTERY_CHANNEL);
    RadioCommand   rc      = RadioCommand();
    VideoFeedback  video   = VideoFeedback(640, 480, &battery, &rc);

    video.start();
    rc.start();
    battery.start();

    std::cout << "Ready !" << std::endl;

    rc.stop();
    video.stop();
    battery.stop();

    return 0;
}

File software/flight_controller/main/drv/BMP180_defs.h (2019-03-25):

#pragma once                      

#include <stdint.h>

/***************************************************************/
/* 	I2C ADDRESS DEFINITION OF BMP180                           */
/***************************************************************/

/* BMP180 I2C Address*/
#define BMP180_I2C_ADDR		(0xEE>>1)

/***************************************************************/
/*	ERROR CODE DEFINITIONS                                     */
/***************************************************************/

#define E_BMP_NULL_PTR				((s8)-127)
#define E_BMP_COMM_RES				((s8)-1)
#define E_BMP_OUT_OF_RANGE			((s8)-2)

/***************************************************************/
/*	CONSTANTS                                                  */
/***************************************************************/

#define BMP180_RETURN_FUNCTION_TYPE                 s8
#define BMP180_INIT_VALUE						    ((u8)0)
#define BMP180_INITIALIZE_OVERSAMP_SETTING_U8X	    ((u8)0)
#define BMP180_INITIALIZE_SW_OVERSAMP_U8X			((u8)0)
#define BMP180_INITIALIZE_NUMBER_OF_SAMPLES_U8X	    ((u8)1)
#define BMP180_GEN_READ_WRITE_DATA_LENGTH			((u8)1)
#define BMP180_TEMPERATURE_DATA_LENGTH			    ((u8)2)
#define BMP180_PRESSURE_DATA_LENGTH				    ((u8)3)
#define BMP180_SW_OVERSAMP_U8X					    ((u8)1)
#define BMP180_OVERSAMP_SETTING_U8X				    ((u8)3)
#define BMP180_2MS_DELAY_U8X			            (2)
#define BMP180_3MS_DELAY_U8X			            (3)
#define BMP180_AVERAGE_U8X			                (3)
#define BMP180_INVALID_DATA			                (0)
#define BMP180_CHECK_DIVISOR			            (0)
#define BMP180_DATA_MEASURE			                (3)
#define BMP180_CALCULATE_TRUE_PRESSURE		        (8)
#define BMP180_CALCULATE_TRUE_TEMPERATURE		    (8)
#define BMP180_SHIFT_BIT_POSITION_BY_01_BIT			(1)
#define BMP180_SHIFT_BIT_POSITION_BY_02_BITS		(2)
#define BMP180_SHIFT_BIT_POSITION_BY_04_BITS		(4)
#define BMP180_SHIFT_BIT_POSITION_BY_06_BITS		(6)
#define BMP180_SHIFT_BIT_POSITION_BY_08_BITS		(8)
#define BMP180_SHIFT_BIT_POSITION_BY_11_BITS		(11)
#define BMP180_SHIFT_BIT_POSITION_BY_12_BITS		(12)
#define BMP180_SHIFT_BIT_POSITION_BY_13_BITS		(13)
#define BMP180_SHIFT_BIT_POSITION_BY_15_BITS		(15)
#define BMP180_SHIFT_BIT_POSITION_BY_16_BITS		(16)


/***************************************************************/
/*	REGISTER ADDRESS DEFINITION                                */
/***************************************************************/

/*register definitions */

#define BMP180_PROM_START__ADDR		 (0xAA)
#define BMP180_PROM_DATA__LEN		 (22)

#define BMP180_CHIP_ID_REG			 (0xD0)
#define BMP180_VERSION_REG			 (0xD1)

#define BMP180_CTRL_MEAS_REG		 (0xF4)
#define BMP180_ADC_OUT_MSB_REG		 (0xF6)
#define BMP180_ADC_OUT_LSB_REG		 (0xF7)

#define BMP180_SOFT_RESET_REG		 (0xE0)

/* temperature measurement */
#define BMP180_T_MEASURE			 (0x2E)
/* pressure measurement*/
#define BMP180_P_MEASURE			 (0x34)
/* TO be spec'd by GL or SB*/
#define BMP180_TEMP_CONVERSION_TIME  (5)

#define BMP180_PARAM_MG		         (3038)
#define BMP180_PARAM_MH		         (-7357)
#define BMP180_PARAM_MI		         (3791)

/***************************************************************/
/*	ARRAY SIZE DEFINITIONS                                     */
/***************************************************************/

#define	BMP180_TEMPERATURE_DATA_BYTES	(2)
#define	BMP180_PRESSURE_DATA_BYTES		(3)
#define	BMP180_TEMPERATURE_LSB_DATA		(1)
#define	BMP180_TEMPERATURE_MSB_DATA		(0)
#define	BMP180_PRESSURE_MSB_DATA		(0)
#define	BMP180_PRESSURE_LSB_DATA		(1)
#define	BMP180_PRESSURE_XLSB_DATA		(2)

#define	BMP180_CALIB_DATA_SIZE			(22)
#define	BMP180_CALIB_PARAM_AC1_MSB		(0)
#define	BMP180_CALIB_PARAM_AC1_LSB		(1)
#define	BMP180_CALIB_PARAM_AC2_MSB		(2)
#define	BMP180_CALIB_PARAM_AC2_LSB		(3)
#define	BMP180_CALIB_PARAM_AC3_MSB		(4)
#define	BMP180_CALIB_PARAM_AC3_LSB		(5)
#define	BMP180_CALIB_PARAM_AC4_MSB		(6)
#define	BMP180_CALIB_PARAM_AC4_LSB		(7)
#define	BMP180_CALIB_PARAM_AC5_MSB		(8)
#define	BMP180_CALIB_PARAM_AC5_LSB		(9)
#define	BMP180_CALIB_PARAM_AC6_MSB		(10)
#define	BMP180_CALIB_PARAM_AC6_LSB		(11)
#define	BMP180_CALIB_PARAM_B1_MSB		(12)
#define	BMP180_CALIB_PARAM_B1_LSB		(13)
#define	BMP180_CALIB_PARAM_B2_MSB		(14)
#define	BMP180_CALIB_PARAM_B2_LSB		(15)
#define	BMP180_CALIB_PARAM_MB_MSB		(16)
#define	BMP180_CALIB_PARAM_MB_LSB		(17)
#define	BMP180_CALIB_PARAM_MC_MSB		(18)
#define	BMP180_CALIB_PARAM_MC_LSB		(19)
#define	BMP180_CALIB_PARAM_MD_MSB		(20)
#define	BMP180_CALIB_PARAM_MD_LSB		(21)


/***************************************************************/
/*	STRUCTURE DEFINITIONS                                      */
/***************************************************************/
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

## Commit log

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2019-03-04 [meca] Add FreeCAD and sizing files
    [quadcopter-calibration-clip.fcstd, quadcopter-calibration-plate.fcstd, quadcopter-gimbal-rail-holder-blind-battery.FCStd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]
2019-03-04 [soft] Add AHRS test program
    [time-gyr-acc-mag-reduit.csv, time-gyr-acc-mag.csv]
2019-03-04 [soft] Add height observer test program
    [time-acc-baro.csv]
2019-03-11 [meca] Add calibration pods CAD
    [quadcopter_calibration_pod.fcstd, quadcopter_calibration_pod_locker.fcstd, quadcopter_calibration_pod_yaw.fcstd]
2019-03-18 Add hardawre
    [quadcopter.kicad_pcb, quadcopter.sch]
2019-03-18 [hardware] Finished schematic and 10dof footprint
    [quadcopter-2019-03-11-10-41-00.sch]
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2019-03-18 [hardware] Generate netlist
    [quadcopter.sch]
2019-03-18 [hardware] PCB 1.0
    [quadcopter.kicad_pcb, quadcopter.sch]
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2019-03-25 [soft] Refacto height observer based on Kalman filter
2019-03-25 [soft] temp fix API break
    [barometer.cpp]
2019-04-02 [meca] Add gimbal-rail-holder-blind-ultrasound CAD
    [quadcopter-gimbal-rail-holder-blind-ultrasound.FCStd]
2019-04-22 [soft] Fix BMP driver + add barometer hal
    [BMP180.cpp, barometer.cpp]
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2019-04-28 [soft] Fix wifi build
    [main.cpp]
2019-05-07 [soft] Replace float variables by double
    [HMC5883L.cpp, MPU6050.cpp, imu.cpp]
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2019-06-08 [soft] Fix type in gpio
    [gpio.cpp]
2019-06-08 [soft] fix motors pulse management
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2019-06-08 [soft] Fix ultrasound sensor management
    [HCSR04.cpp]
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2019-06-08 [soft] Update the ultrasound sensor covariance depending on height
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2019-06-08 [soft] Add PID update endpoint in controller API
2019-06-08 [soft] Set motors speed to 0 at boot
2019-06-08 [soft] Prevent bad motors throttle value and mid-throttle stalling
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2019-06-08 [soft] Invert pitch control commands in mixer
2021-06-21 Bump ESP-IDF to v4.2 + required migration
    [partitions.csv]
2021-06-21 [ESC] Replace motor command with dshot
    [DShotRMT.cpp]
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2021-07-24 [PID] Fix derivate implementation
2021-07-24 [sensors] Add multi-bytes I2C operations to reduce reading duration
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2021-07-24 [IMU] Reduce hardware lowpass cutoff frequency to 98 Hz
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2021-07-24 [attitude controller] Fix registry PID coeffs init and update
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2021-07-24 [PID] Fix missing filter d_term filter init
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2021-07-24 [Camera controller] Add skeleton for registry values init
2021-07-24 [Battery supervisor] Add skeleton for registry values init
2021-07-24 [Tests] Add gyro noise measurement data
    [thurst_frequency.csv]
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2021-08-13 [PID] Use proper word 'setpoint' instead of 'consign'
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2021-08-13 [Mixer] Fix inverted yaw command (props in/out)
2021-08-13 [data model] update with kff and roll/pitch speed mode for PID tuning
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2021-08-13 [attitude controller] Remove PID tuning data model binding
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2021-08-15 [base_station] Add scope config for graphical PID tuning
    [quadcopter_udp_pid.json]
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2021-11-03 [pulse] Fix timer configuration
2021-11-03 [tests] Add notebook for height_observer Kalman filter testing and tuning
    [height_dynamic.csv, height_static.csv]
2021-11-04 [tests] Add gps and filters testing notebooks
    [data.csv]
2021-11-11 [UART] Improve uart class
    Mostly in order to handle pattern detection events
2021-11-11 [UART] Use project custom logging
    and increase task stack to handle this new logging
2021-11-11 [UART] Use project custom task
    and modify main accordingly
2021-11-11 [DATA] Use filesystem to read data model
    and upload the storage image folder each time the ESP32 is flashed
    [partitions.csv]
2021-11-11 [NMEA] Add NMEA controller into main
    and plug it with registry and uart pattern detection callback
2021-11-11 [UART] Use project custom queue
    and move queue template functions into header file, add a typedef for freeRTOS queue handle to avoid using it outside this wrapper, add a constructor based on a queue handle, add an "empty" function and fix "pop" & "push" functions
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2021-11-11 [GPS] Init UART and start pattern matcher from GPS class
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2021-11-11 Fix build in data recording mode
    [main.cpp]
2021-11-11 [motors] Add dedicated motor_controller for manual motor control
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2021-11-11 [rate ctrl] rename and fix dynamic RPM notch filter
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2021-11-19 [registry] Prevent stack overflow at loading
    [data_ressources_registry.cpp]
2021-11-19 [pid] remove debug as it is replaced by telemetry
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2021-11-19 [uart] fix GPS decoding error by preventing flushing received following bytes at pattern detection
2022-01-14 [sdkconfig] Set RTOS timer service to max priority
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2022-01-14 [gyro] Move gyro calibration sequence after init (when drone don't move)
2022-01-14 [uart] tune queues length and fix pattern detector
2022-01-14 [GPS] Replace new NMEA sequence polling by rtos queue
    [gps.cpp]
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2022-01-24 [attitude ctrl] Fix invalid min and max PID output commands
2022-01-24 [PID] Replace error derivate by input derivate to ignore setpoints steps
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2022-01-27 [scope] Move and rename scope configs
    [quadcopter_udp_pid.json]
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2022-01-27 [attitude ctrl] Add slew filters on attitude controllers command (rate setpoints, ie. limit angular acceleration)
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2022-01-27 [rate ctlr] Fix bad gyro calibration correction
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2022-01-27 [rate ctlr] Add accelero bias correction with calibration
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2022-02-01 [PID] Add state reset method and call it when controllers are disabled
2022-02-01 [height ctlr] TEMPORARY - Use ultrasound sensor height instead of Kalman filter output
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2022-02-16 [GPIO] Fix gpio init for pins 33-36
    [gpio.cpp]
2022-02-16 [SPI] Fix spi init with explicit flags initialization
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2022-02-18 [height observer] Kalman filter tuning and working
    [height_dynamic.csv, height_static.csv]
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2022-03-03 [SI4432] Tune config for working RX
    [Si4432-Register-Settings_RevV-v26.xls]
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2022-03-10 [radio] Stabilize python radio driver and broker
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2022-03-10 [radio] Create radio broker
    [main.cpp, platform.h]
2022-03-10 [broker] Centralize broker channels and use thoses definitions for UDP
    [main.cpp, platform.h]
2022-03-10 [Heartbeat] Use radio broker with proper channel for heartbeat sending
    [main.cpp]
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2022-03-10 [radio command] Register channel to radio broker and listen from both UDP and radio
    [main.cpp]
2022-03-10 [radio command Add failsafe commands in case of reception lost
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2022-03-26 [height observer] Tuning & restoring zero velocity detector to improve stability
    [height_dynamic.csv, height_static.csv]
2022-04-01 [tasks] Add missing includes for task delay
    [BMP180.cpp]
2022-04-01 [radio] Remove broker mechanisms from radio and convert to lower level abstraction layer
    [main.cpp, platform.h]
2022-04-01 [broker] Create broker for UDP and radio communication channels multiplexing
    [main.cpp, platform.h]
2022-04-01 [logger] User broker instead of UDP server for logs streaming
    [main.cpp, platform.h]
2022-04-01 [Heartbeat] Use broker instead of out-of-date Udp server and radio broker
    [main.cpp, platform.h]
2022-04-01 [data model ctrl] Centralize json and binary requests handling in ctlr which relies on broker
    [main.cpp, platform.h]
2022-04-01 [Heartbeat] Increase period to 3 sec to avoid radio collisions
    [platform.h]
2022-04-01 [registry] Fix binary id to string key lookup
    [data_ressources_registry.cpp]
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2022-04-03 [wifi] Replace default wifi config with action camera credentials
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2022-05-01 Move flight controller
    [partitions.csv, time-acc-baro.csv, time-gyr-acc-mag-reduit.csv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]
2022-05-01 Move test & tools
    [data.csv, height_dynamic.csv, height_static.csv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]
2022-05-01 Move 3D
    [gimbal-rail-holder-blind-battery.FCStd, gimbal-rail-holder-blind-ultrasound.FCStd, gimbal-rail-holder-blind.FCStd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]
2022-05-01 Move sizing
    [sizing.xlsx]
2022-05-01 Move quadcopter PCB
    [quadcopter-2019-03-11-10-41-00.sch, quadcopter.kicad_pcb, quadcopter.kicad_sch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]
2022-05-01 Move flight_controller PCB
    [quadcopter.kicad_sch]
2022-05-01 [PCB] Add remote PCB v1.0
    [remote.kicad_pcb, remote.kicad_sch, remote.sch]
2022-05-01 [GPS] Fix missing initializer warning
    [gps.cpp]
2022-05-02 [3D] Add quadcopter antennas holders
    [gps_antenna_holder.fcstd, rf_antenna_holder.fcstd, rf_board_holder.fcstd]
2022-05-02 [3D] Add remote top
    [remote_top.fcstd]
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2022-05-24 [radio command] Fix sticks ADC channels
2022-05-24 [radio command] Fix I2C port
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2022-05-24 [I2C] Fix I2C write method with a single transfer
2022-05-24 [radio command] Fix SPI unused include
2022-05-24 [radio command] replace printf with iostream operators
    [SI4432.cpp]
2022-05-24 [radio command] Fix buttons GPIO mapping
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2022-06-11 [3D] Add landing system pieces
    [land_foot.fcstd, landing_leg_T.fcstd, landing_leg_holder.fcstd]
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2022-06-17 [rc] Fix gpio shared memory access denied permission
    [gpio.cpp]
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2022-06-17 [3D] Update landing leg holder with transversal junction
    [landing_leg_holder.fcstd]
2022-06-17 [3D] Add remote usb hub and batery support
    [hub_battery_support.fcstd]
2022-06-17 [3D] Add remote backcover
    [Backcover_Remote_v17.stl]
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2022-06-19 [rc] Enter in range test mode when pressing both bottom buttons at startup
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2022-06-25 [fc + rc] Add camera record request and gimbal tilt in radio commands
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2022-06-25 [flight controller - radio] Add mutex on tx and rx packet in driver
2022-06-25 [rc] Fix spi bulk registers read
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2022-07-25 [3D] Add vtx support 3D model
    [vtx.fcstd, vtx.stl]
2022-07-27 [3D] Add exported stl models
    [battery_hub_support.stl, gimbal_rail_holder_blind.FCStd, gimbal_rail_holder_blind.stl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]
